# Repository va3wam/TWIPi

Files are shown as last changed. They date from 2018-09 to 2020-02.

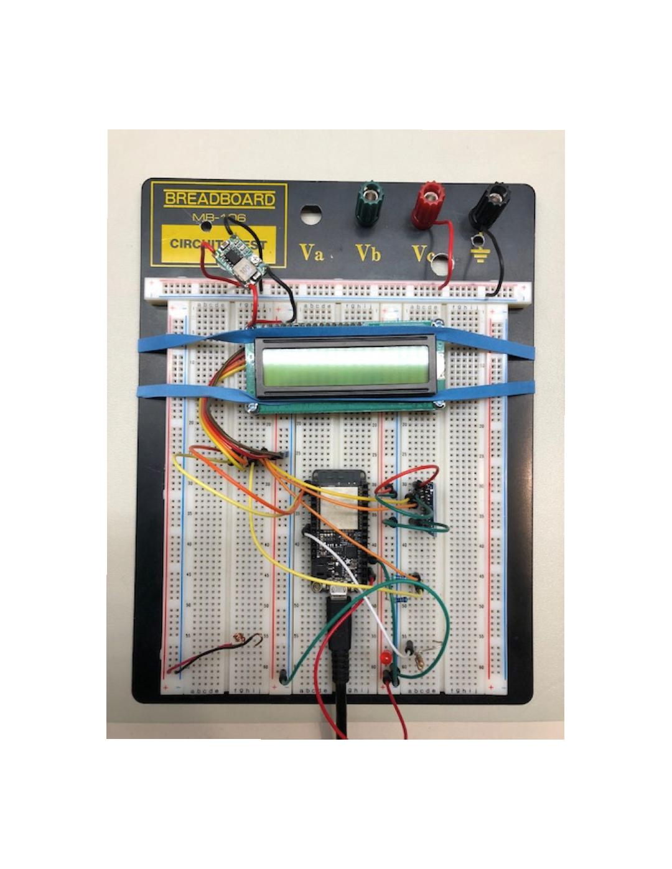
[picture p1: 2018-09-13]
img/SegbotStepMARK3.jpg

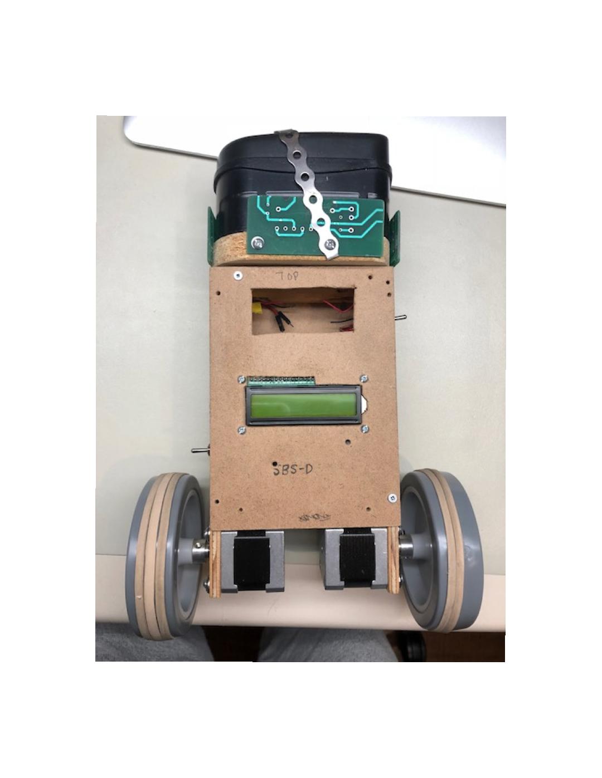
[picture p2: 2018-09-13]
img/SegbotStepMARK2.jpg

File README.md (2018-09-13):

# TWIPi
This repository contains all the information on the fourth iteration of the SegbotSTEP family of robot designs. This repository contains C++ source code intended to run on the Adafruit Huzzah32 development board; Java code intended to run on a remote client such as a MAC or PC; EagleCAD schematic and layout files containing the circuit designs of the robot; Fusion 360 files (or pointers to those files on the AutoCAD cloud) used to mill the robot chassis; and all the libraries used by the IDEs that make up the tool chain used to create the robot.  

## Getting Started

Full details about this project can be read on our [wiki](https://github.com/va3wam/TWIPi/wiki). 

### Prerequisites

In order to make use of the robot circuit board and schematic diagrams you will need AutoCAD's EagleCAD application. In order to make use of the CAD and CAM diagrams of the robot chassis you will need AutoCAD's Fusion 360 application. From a software perspective, the Java and C++ (Arduino) code was written using Microsoft's Visual Source Code IDE.

### SOC Hardware Compatability

The Arduino C++ code was written to run on the Espressif ESP WROOM32 "Software On a Chip" (SOC). The development board used for this SOC is the Adafruit Huzzah32 featherboard.  

```
Note that this code will NOT run on an ESP8266. 
```

### Other Hardware Compatability

Aside from the code and development you will need to build a TWIPi compatible chassis and PCB. This
repository has EagleCAD diagrams to help you build the PCB. Also included are Fusion360 
CAD/CAM diagrams and associated GCODE for a Tormach 770 CNC mill to create the robot chassis. 
Full details for this project are located on the wiki associated with this repository.

### Installing

There are numerous tutorials on how to install Arduino code onto an ESP WROOM32 from Visual Source Code. Details and relevant links can be found on this respositories wiki. 

## Running the tests

At this time there are no automated tests for this system

## Deployment

This Arduino code was developed using the following set up.

### Built With

* [Visual Studio Code](https://code.visualstudio.com/) - The IDE
* [Platformio](https://platformio.org/) - Editor plugin
* Library Framework - Arduino
* Hardware platform - espressif32
* Board - Adafruit Huzzah32 featherboard
### Arduino Libraries
The following additional libraries are used in the Arduino C++ code:
* https://github.com/Pedroalbuquerque/ESP32WebServer
* https://github.com/Links2004/arduinoWebSockets
* https://github.com/marcoschwartz/LiquidCrystal_I2C
* https://github.com/bblanchon/ArduinoJson

## Contributing

This project is being developed by a couple of buddies. We are tracking the tasks for this
effort in a series of small [projects](https://github.com/va3wam/TWIPi/projects).

## Versioning

We use [SemVer](http://semver.org/) for versioning. For the versions available, see the [tags on this repository](https://github.com/va3wam/TWIPi/branches/all). 

## Authors

* [Doug](https://github.com/nerdoug) - *PID and motor control logic and circuit diagrams*
* [Andrew](https://github.com/va3wam) - *Initial code porting from ESP128 to ESP32, remote Java client and CAD/CAM designs* 

See also the list of [contributors](https://github.com/va3wam/TWIPi/graphs/contributors) who participated in this project.

## License

This project has no licensing terms. Use at own risk, no support provided. 

## Acknowledgments

* Big thanks to [Brokking](http://www.brokking.net/yabr_main.html) for his excellent tutorial which really helped us get going
* Thanks to the folks who developed the libraries we have made use of for I2C, JSON, Web and Websockets

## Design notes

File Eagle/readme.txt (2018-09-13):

This is the directory where PCB files are placed

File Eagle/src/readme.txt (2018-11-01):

This is where the Schematic (SCH) and Layout (BRD) files for Eagle PCBs go. the file testToolOffsetModForFlatCAMfiles.nc contains manually crafted g-code to test ATC control for jobs created in FlatCAM. See TWIPi\Eagle\docConvertFlatCAMgcode.ods for the procedure for inserting these codes into FlatCAM generated G-code.

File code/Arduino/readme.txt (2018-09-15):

This is where c++ code intended to run on the Arduino compliant SOC goes

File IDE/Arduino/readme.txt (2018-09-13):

This is where Arduino IDE configuration and library files go

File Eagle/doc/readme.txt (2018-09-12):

This directory contains the PCB files associated with the TWIPi project

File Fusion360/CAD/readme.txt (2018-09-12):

This directory contains the CAD files associated with the TWIPi project

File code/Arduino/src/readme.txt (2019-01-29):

This is where the C++ code loaded onto the ESP32 inside the robot is located.

TWIPi directory has the code to be loaded onto the ESP32 that runs the TWIPi robot
BlinkLED directory has code that blinks the software controlled LED (white) on the TWIPi peripheral board
LCD16x2Test directory has code that prints "HELLO WORLD" on TWIPi's LCD
two-I2C-scan directory has code that scans the two I2C buses for active devices

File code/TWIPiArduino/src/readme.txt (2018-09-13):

This is where the C++ code loaded onto the ESP32 inside the robot is located.

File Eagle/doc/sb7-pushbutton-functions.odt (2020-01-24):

Twipi Pushbutton Functions

Layout:

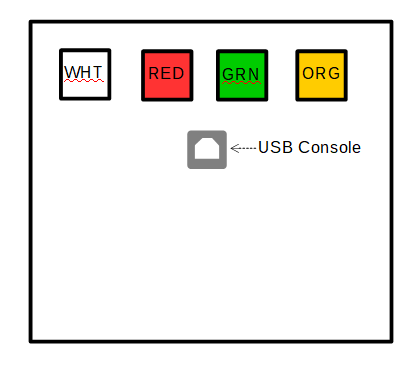
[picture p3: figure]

Functions

Button Colour | Pushed In | Out Position | Illuminated | Extinguished
White | Battery Power CONNECTED | Battery power DISCONNECTED | 12 V power IS available | 12 V power IS NOT available
Red | 5 v power comes from BATTERY | 5 v power comes from USB Console | 5 V battery power IS available | 5 V battery power is NOT available
Green | ESP32 is being RESET | ESP32 is NOT being RESET | Selected 5 V power is going to ESP32 | Selected 5 V power is NOT going to ESP32
Orange | S/W readable pin is HIGH | S/W readable pin is LOW | S/W has turned ON the light | S/W has turned OFF the light

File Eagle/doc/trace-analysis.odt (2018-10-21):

Examination of Etch Widths In Eagle > FlatCAM > G-CodeFiles

Test files:

etch-fun.sch, etch-fun.brd

-Eagle files for minimal circuiit to simplify analysis

tst1-trace-by-wiki.nc, tst1-drill-by-wiki.nc

-G-Code files produced from etch-fun files by following procedure and parameter settings in our wiki.

- parameter settings are documented in the cad-conversions.ods file as well

chart-data.ods

- import of trace file G-Code corners into a spreadsheet

- charted using a scatter graph to allow examination of data points from the shapes

The bottom right corner of the circuit has a trace running between the larger of the pads which seems like a good case to examine. The scatter graph for that part looks like this:

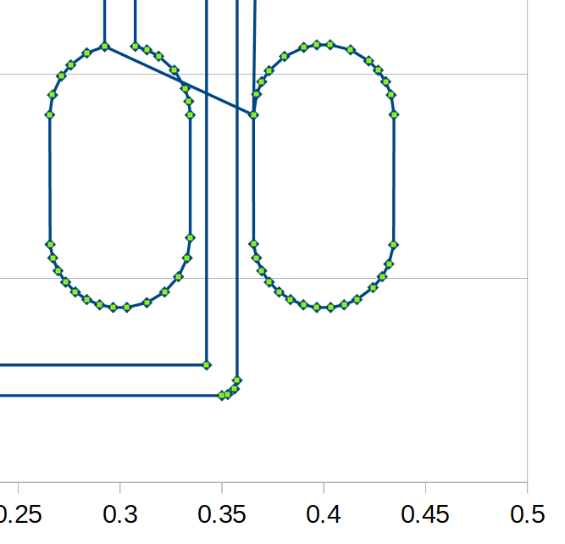
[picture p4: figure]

The cross section of the vertical trace looks like this:

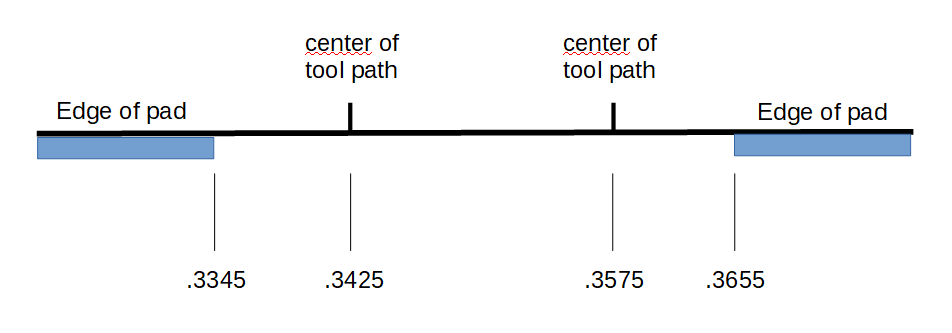
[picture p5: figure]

Adding the 0.009 inch width of the V bit to the diagram, we get:

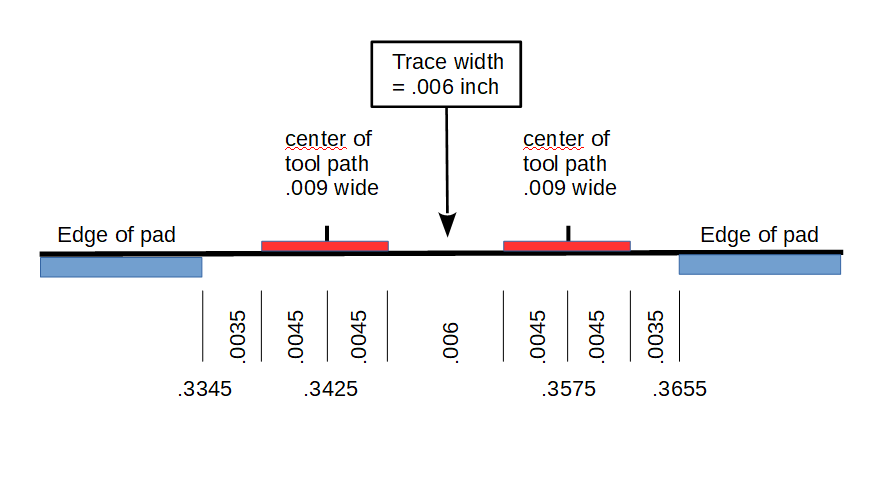
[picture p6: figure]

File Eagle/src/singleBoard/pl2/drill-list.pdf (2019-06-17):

Sheet1

Page 1

Component / Package | Comment
Board Mounting holes | 1 | 4 | 2.845 | 112 | 0.112 | 4 | A
Power cable headers | 2 | 2 | 1.016 | 40 | 0.04 | 4 | B
Ribbon cable connector | 1 | 16 | 0.9144 | 36 | 0.036 | 16 | B
Pushbutton switches | 4 | 5 | 1.2 | 47.2 | 0.0472 | 20 | C
USB Jack | 1 | 4 | 0.92 | 36.2 | 0.0362 | 4 | B | cable pins
USB Jack | 1 | 2 | 2.3 | 90.6 | 0.0906 | 2 | A | mounting lugs
Diodes | 2 | 2 | 1.4986 | 59 | 0.059 | 4 | D
1 pin headers / Vias | 13 | 1 | 1 | 39.4 | 0.0394 | 13 | B
total holes: | 67
Suggested Drill Sizes in column H: | A | 112 mils
| | | B | 38 mils
| | | C | 47 mils
| | | D | 59 mils

`

Component
Qty

Holes per
component

Hole size
mm

Hole size
mils

Hole size
inches

total
hole count

Standard
-ized

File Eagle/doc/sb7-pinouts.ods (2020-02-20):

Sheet: ESP32 connections
PINOUTS FOR THE Adafruit ESP32 Feather Module in the TWIPi Single Board Version 7 (SB7)
Adafruit ESP32 Phys. pin | Gpio | Pin Function (A/D, I2C, SPI, serial...) | Connection in the Single Board Version 3 (SB3)
1 |  | RESET | XB1 - Reset switch - to Normally Open (NO) on 3rd pushbutton (green)
2 |  | 3V | P6 on both DRV’s (JP19>JP15, JP20>JP16),IMU Vcc, IMU I2C pullups, CPU & IMU decoupling cap,XB2
3 |  | n/c
4 |  | CPU GND | Bridged GNDs: battery gnd, 12V, 5V bat., 5V USB, ESP-USB, DRV, CPU & IMU decoupl, XB12 & 14, LCD, Mosfet
5 | 26 | A0, GPio26 | n/c
6 | 25 | A1, GPio25 A/D | (A/D input) to centre between the 2 resistors of the MOSFET controlled voltage divider
7 | 34 | A2, GPio34 | n/c
8 | 39 | A3, GPio39 | INT pin on IMU - generates an interrupt
9 | 36 | A4, GPio36 | n/c
10 | 4 | A5, GPio4 | XB3 software-readable pushbutton input, to COM position on 4th pushbutton
11 | 5 | SPI-SCK, GP05 | MOSFET enable on battery monitor (Gate)
12 | 18 | SPI-MO | DRV1-STEP
13 | 19 | SPI-MI | DRV1-DIR
14 | 16 | RX Serial1 | DRV1-ENA
15 | 17 | TX Serial1 | I2C-IMU Pin4, SDA with 2.2K pullup to 3.3V
16 | 21 | GPio21 | I2C-IMU Pin3, SCL with 2.2K pullup to 3.3V
17 | 23 | I2C, GP23 | XB4 > software controlled LED, +ve LED input on 4th pushbutton (orange)
18 | 22 | I2C, GP22 | I2C-LCD-SDA-P2 (4.7K pullup to 5V)
19 | 14 | A6, GPio14 | I2C-LCD-SCL-P1 (4.7K pullup to 5V)
20 | 32 | A7, GPio32 | DRV2-FAULT Input (used to be VDD on old A4988)
21 | 15 | A8, GPio15 | DRV2-DIR
22 | 33 | A9, GPio33 | DRV2-STEP
23 | 27 | A10, GPio27 | DRV2-ENA
24 | 12 | A11, GPio12 | N/C. Using this pin seems to prevent software download in some circumstances
25 | 13 | A12, GPio13 | DRV1-FAULT Input. (used to be VDD on old A4988)
26 |  | USB | +5 Volts, LCD-I2C pullups, LCD header
27 |  | Enable | n/c
28 |  | LiPo Battery | n/c
 | (A13,GPio35) resistor divider linked to VBAT
 |  |  | fully programmable weak pullup / pulldown ( 14, 16, 17, 18, 19, 21, 22, 23)
 |  |  | powers up with weak pullUP enabled ( 5, 15)
 |  |  | powers up with weak pullDOWN enabled ( 4)
 |  |  | input only pins ( 34, 36, 39)
 |  |  | can be touch capacitive sensor ( 10, 19, 20, 21, 22, 23, 24, 25)
DRV stands for the DRV8825 stepper motor controllers. DRV1 is the top DRV (closest to IMU), DRVR is the bottom DRV,

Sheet: MB LCD Header
LCD Header on Main Board
 | LCD Hdr - 1 | SCL
 | LCD Hdr - 2 | SDA
 | LCD Hdr - 3 | 5 V
 | LCD Hdr - 4 | GND
 | above agrees with order of pins on standard LCD 1602

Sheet: MB CPU Console USB Cable
CPU Console USB cable - Micro USB to 4 pin header on MB
Actual | Standard | Pin # | Function
ORG | RED | MB-USB-Hdr-1 | IBC22 - +5 Common
YEL | WHT | MB-USB-Hdr-2 | IBC23 - USB Jack - 2 - D-
GRN | GRN | MB-USB-Hdr-3 | IBC24 - USB Jack - 3 - D+
BLU | BLK | MB-USB-Hdr-4 | IBC25 - Gnd Common

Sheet: USB Reference
reference: http://www.hobbytronics.co.uk/usb-connector-pinout

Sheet: Standard LCD 1602 I2C Wiring
 |  | ------- | GND
 |  | ------- | 5 V
 |  | ------- | SDA
 |  | ------- | SCL
 | Back View
Industry standard pinout for LCD 1602 I2C interface.
sample references:
http://wiki.sunfounder.cc/index.php?title=I%C2%B2C_LCD1602
https://opencircuit.nl/ProductInfo/1000061/I2C-LCD-interface.pdf

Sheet: MPU-6050
http://acoptex.com/project/118/basics-project-020a-mpu-6050-gy-521-gy-521-module-3-axis-gyroscope-and-accelerometer-at-acoptexcom/
 | MPU-6050 is mounted on the GY-521 board with:
 | -MPU-6050 on component side of board, in about the center
 | - the +Y axis pointing towards short side of board touching Vcc
 | - the +X axis pointing towards the long side of the board closest to the mounting holes
 | - the +Z axis pointing upwards, perpendicular to the component side
 | - the label text on the MP-6050 chip is in the same direction as the Vcc label in the silkscreen
 | in MB2 hardware, the IMU is mounted “upside down, and rotated”:
 | +Y axis pokes out of robot's chest
 | +X axis pokes out of bot's right shoulder (viewer's left)
 | +Z axis points towards ground
 | The pins leave the IMU on the solder side of the board, not the side with the IMU
 | - the label text on the MP-6050 chip is in the same direction as the Vcc label in the silkscreen

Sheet: pushbutton wiring
See other stand alone documents

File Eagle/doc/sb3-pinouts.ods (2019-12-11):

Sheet: ESP32 connections
PINOUTS FOR THE Adafruit ESP32 Feather Module in the TWIPi Single Board Version 3 (SB3)
Adafruit ESP32 Phys. pin | Gpio | Pin Function (A/D, I2C, SPI, serial...) | Connection in the Single Board Version 3 (SB3)
1 |  | RESET | XB1 - Reset switch
2 |  | 3V | P6 on both DRV’s (JP19>JP15, JP20>JP16),IMU Vcc, IMU I2C pullups, CPU & IMU decoupling cap,XB2
3 |  | n/c
4 |  | CPU GND | Bridged GNDs: battery gnd, 12V, 5V bat., 5V USB, ESP-USB, DRV, CPU & IMU decoupl, XB12 & 14, LCD, Mosfet
5 | 26 | A0, GPio26 | n/c
6 | 25 | A1, GPio25 A/D | (A/D input) JP2 > JP1 > MOSFET controlled voltage divider
7 | 34 | A2, GPio34 | n/c
8 | 39 | A3, GPio39 | n/c
9 | 36 | A4, GPio36 | n/c
10 | 4 | A5, GPio4 | XB3 software-readable puchbutton input
11 | 5 | SPI-SCK, GP05 | DRV1-ENA (powers up with WPD enabled)
12 | 18 | SPI-MO | DRV1-STEP
13 | 19 | SPI-MI | DRV1-DIR
14 | 16 | RX Serial1 | MOSFET enable on battery monitor
15 | 17 | TX Serial1 | I2C-IMU Pin4, SDA with 2.2K pullup to 3.3V
16 | 21 | GPio21 | I2C-IMU Pin3, SCL with 2.2K pullup to 3.3V
17 | 23 | I2C, GP23 | XB4 > software controlled LED
18 | 22 | I2C, GP22 | I2C-LCD-SDA-P1 (4.7K pullup to 5V)
19 | 14 | A6, GPio14 | I2C-LCD-SCL-P2 (4.7K pullup to 5V)
20 | 32 | A7, GPio32 | DRV2-FAULT Input
21 | 15 | A8, GPio15 | DRV2-DIR
22 | 33 | A9, GPio33 | DRV2-STEP
23 | 27 | A10, GPio27 | DRV2-ENA
24 | 12 | A11, GPio12 | DRV1-FAULT Input. Trace to ESP Pin 24 was cut because it prevented code download. Could use pin 7, 8 or 9
25 | 13 | A12, GPio13 | n/c
26 |  | USB | +5 Volts, LCD-I2C pullups, LCD header
27 |  | Enable | n/c
28 |  | LiPo Battery | n/c
 | (A13,GPio35) resistor divider linked to VBAT
 |  |  | fully programmable weak pullup / pulldown ( 14, 16, 17, 18, 19, 21, 22, 23)
 |  |  | powers up with weak pullUP enabled ( 5, 15)
 |  |  | powers up with weak pullDOWN enabled ( 4)
 |  |  | input only pins ( 34, 36, 39)
 |  |  | can be touch capacitive sensor ( 10, 19, 20, 21, 22, 23, 24, 25)
DRV stands for the DRV8825 stepper motor controllers. DRV1 is the top DRV (closest to IMU), DRVR is the bottom DRV,

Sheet: TWIPi External Switches Connector
PINOUTS for the 16 pin External Switch Connector (XB)
Physical Pin | Pushbutton function name | Function
XB1 | PC8 | ESP32 Reset Pin
XB2 | PC10 | 3.3 V
XB3 | PC11 | s/w readable switch input on ESP10, GPio4
XB4 | PC9 | s/w controlled LED on ESP17, GPio23
XB5 | PC1 | thru resistor to 12V for LED monitor
XB6 | KEY | unused. blocked to prevent incorrect insertion
XB7 | PC5 | 5V from regulator, for monitor LED
XB8 | PC6 | 5V from USB jack
XB9 | PC7 | to ESP32 USB 5V
XB10 | UJ1 | USB Jack pin 1
XB11 | UJ2 | USB Jack pin 2
XB12 | PC4 | Ground
XB13 | UJ3 | USB Jack pin 3
XB14 | UJ4 | USB Jack pin 4
XB15 | PC2 | Battery’s positive side 20+ Volts

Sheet: MB LCD Header
LCD Header on Main Board
 | LCD Hdr - 1 | SCL (pin 1 nearest ESP32)
 | LCD Hdr - 2 | SDA
 | LCD Hdr - 3 | 5 V
 | LCD Hdr - 4 | GND
 | above agrees with order of pins on standard LCD 1602

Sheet: MB CPU Console USB Cable
CPU Console USB cable - Micro USB to 4 pin header on MB
Actual | Standard | Pin # | Function
ORG | RED | MB-USB-Hdr-1 | IBC22 - +5 Common
YEL | WHT | MB-USB-Hdr-2 | IBC23 - USB Jack - 2 - D-
GRN | GRN | MB-USB-Hdr-3 | IBC24 - USB Jack - 3 - D+
BLU | BLK | MB-USB-Hdr-4 | IBC25 - Gnd Common

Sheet: USB Reference
reference: http://www.hobbytronics.co.uk/usb-connector-pinout

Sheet: Standard LCD 1602 I2C Wiring
 |  | ------- | GND
 |  | ------- | 5 V
 |  | ------- | SDA
 |  | ------- | SCL
 | Back View
Industry standard pinout for LCD 1602 I2C interface.
sample references:
http://wiki.sunfounder.cc/index.php?title=I%C2%B2C_LCD1602
https://opencircuit.nl/ProductInfo/1000061/I2C-LCD-interface.pdf

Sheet: MPU-6050
http://acoptex.com/project/118/basics-project-020a-mpu-6050-gy-521-gy-521-module-3-axis-gyroscope-and-accelerometer-at-acoptexcom/
 | MPU-6050 is mounted on the GY-521 board with:
 | -MPU-6050 on component side of board, in about the center
 | - the +Y axis pointing towards short side of board touching Vcc
 | - the +X axis pointing towards the long side of the board closest to the mounting holes
 | - the +Z axis pointing upwards, perpendicular to the component side
 | - the label text on the MP-6050 chip is in the same direction as the Vcc label in the silkscreen
 | in MB2 hardware, the IMU is mounted “upside down, and rotated”:
 | +Y axis pokes out of robot's chest
 | +X axis pokes out of bot's right shoulder (viewer's left)
 | +Z axis points towards ground
 | The pins leave the IMU on the solder side of the board, not the side with the IMU
 | - the label text on the MP-6050 chip is in the same direction as the Vcc label in the silkscreen

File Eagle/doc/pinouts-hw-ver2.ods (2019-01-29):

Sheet: ESP32 connections
PINOUTS FOR THE Adafruit ESP32 Feather Module Version 3
Adafruit ESP32 Phys. pin | Gpio | Pin Function (A/D, I2C, SPI, serial...) | Connection
1 |  | RESET | IBC24 - Reset switch
2 |  | 3V | P10 on both DRV’s,IMU Vcc, IMU I2C pullups, IMU decoupling cap
3 |  | n/c
4 |  | CPU GND | Bridged GNDs: battery gnd, 12V, 5V bat., 5V USB, ESP32, DRV
5 | 26 | A0, GPio26 | n/c
6 | 25 | A1, GPio25 A/D | (A/D input) JP2 > JP4 > IBC12 > MOSFET controlled voltage divider
7 | 34 | A2, GPio34 | n/c
8 | 39 | A3, GPio39 | n/c
9 | 36 | A4, GPio36 | n/c
10 | 4 | A5, GPio4 | DRVR-ENA (powers up with WPD enabled)
11 | 5 | SPI-SCK, GP05 | JP1 > JP3 > IBC13 > MOSFET enable on battery monitor
12 | 18 | SPI-MO | DRVR-STEP
13 | 19 | SPI-MI | DRVR-DIR
14 | 16 | RX Serial1 | IBC-12 Software readable sense switch (Reset switch held left)
15 | 17 | TX Serial1 | I2C-IMU Pin4, SDA with 2.2K pullup to 3.3V
16 | 21 | GPio21 | I2C-IMU Pin3, SCL with 2.2K pullup to 3.3V
17 | 23 | I2C, GP23 | IBC11 > software controlled LED
18 | 22 | I2C, GP22 | I2C-LCD-SDA-P1 (4.7K pullup to 5V)
19 | 14 | A6, GPio14 | I2C-LCD-SCL-P2 (4.7K pullup to 5V)
20 | 32 | A7, GPio32 | DRVL-DIR
21 | 15 | A8, GPio15 | DRVL-STEP
22 | 33 | A9, GPio33 | DRVL-ENA
23 | 27 | A10, GPio27 | n/c
24 | 12 | A11, GPio12 | n/c
25 | 13 | A12, GPio13 | n/c
26 |  | USB | +5 Volts
27 |  | Enable | n/c
28 |  | LiPo Battery | n/c
 |  | (A13,GPio35) resistor divider linked to VBAT
 |  | fully programmable weak pullup / pulldown ( 14, 16, 17, 18, 19, 21, 22, 23)
 |  | powers up with weak pullUP enabled ( 5, 15)
 |  | powers up with weak pullDOWN enabled ( 4)
 |  | input only pins ( 34, 36, 39)
 |  | can be touch capacitive sensor ( 10, 19, 20, 21, 22, 23, 24, 25)
 |  | DRV stands for the DRV8825 stepper motor controllers (one rotated 180 degrees to simplify circuit layout)
 |  | DRVL is the left DRV, closest to the ESP32. DRVR is the right DRV, closest to the CPU USB header

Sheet: TWIPi InterBoard Connector
 |  | 2018-12-28
PINOUTS for the 25 pin InterBoard Connector (IBC)
25 Pin IBC for PB1A | Pin Function | Connection
1 | 12 V power | Cap1pos-DRVR-VMOT-P16
2 | stepper coil | DRVL-1B-P11
3 | stepper coil | DRVL-1A-P12
4 | stepper coil | DRVL-2A-P13
5 | stepper coil | DRVL-2B-P14
6 | 12 V power | Cap2pos-DRVL-VMOT-P16
7 | 12V GND | Cap2neg-DRVL-MGND-P15
8 | n/c
9 | battery A2D | Vdivider >IBC9 >JP4 >JP2 >ESP6 = A2D A1
10 | MOSFET Enable | Mosfet Gate >IBC10 >JP3 >JP1 > ESP11 = GPio5
11 | s/w controlled LED | CPU-GPio 23, pin 17
12 | s/w sense switch | Reset switch-left-pos > IBC12 > ESP14 = GPio16
13 | RESET | Reset switch-right-pos >IBC13 > CPU-P1
14 | 12V GND | Cap1neg-DRVR-MGND-P15
15 | n/c
16 | n/c
17 | n/c
18 | stepper coil | DRVR-2B-P14
19 | stepper coil | DRVR-2A-P13
20 | stepper coil | DRVR-1A-P12
21 | stepper coil | DRVR-1B-P11
22 | 5V Source Selected | USB JACK Pin1 +5V gets to CPU USB HDR - P1
23 | USB Data | USB JACK Pin2 D-, gets to CPU USB HDR - P2
24 | USB Data | USB JACK Pin3 D+ , gets to CPU USB HDR - P3
25 | USB Ground | USB JACK Pin4 Gnd, gets to CPU USB HDR - P4

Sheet: MB LCD Header
LCD Header on Main Board
 | LCD Hdr - 1 | SCL (pin 1 nearest ESP32)
 | LCD Hdr - 2 | SDA
 | LCD Hdr - 3 | 5 V
 | LCD Hdr - 4 | GND
 | above agrees with order of pins on standard LCD 1602
 | (unlike MB1, which had SDA and SCL reversed)

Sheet: MB CPU Console USB Cable
CPU Console USB cable - Micro USB to 4 pin header on MB
Actual | Standard | Pin # | Function
ORG | RED | MB-USB-Hdr-1 | IBC22 - +5 Common
YEL | WHT | MB-USB-Hdr-2 | IBC23 - USB Jack - 2 - D-
GRN | GRN | MB-USB-Hdr-3 | IBC24 - USB Jack - 3 - D+
BLU | BLK | MB-USB-Hdr-4 | IBC25 - Gnd Common

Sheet: USB Reference
reference: http://www.hobbytronics.co.uk/usb-connector-pinout

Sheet: Standard LCD 1602 I2C Wiring
 |  | ------- | GND
 |  | ------- | 5 V
 |  | ------- | SDA
 |  | ------- | SCL
 | Back View
Industry standard pinout for LCD 1602 I2C interface.
sample references:
http://wiki.sunfounder.cc/index.php?title=I%C2%B2C_LCD1602
https://opencircuit.nl/ProductInfo/1000061/I2C-LCD-interface.pdf

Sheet: MPU-6050
http://acoptex.com/project/118/basics-project-020a-mpu-6050-gy-521-gy-521-module-3-axis-gyroscope-and-accelerometer-at-acoptexcom/
 | MPU-6050 is mounted on the GY-521 board with:
 | -MPU-6050 on component side of board, in about the center
 | - the +Y axis pointing towards short side of board touching Vcc
 | - the +X axis pointing towards the long side of the board closest to the mounting holes
 | - the +Z axis pointing upwards, perpendicular to the component side
 | - the label text on the MP-6050 chip is in the same direction as the Vcc label in the silkscreen
 | in MB2 hardware, the IMU is mounted “upside down, and rotated”:
 | +Y axis pokes out of robot's chest
 | +X axis pokes out of bot's right shoulder (viewer's left)
 | +Z axis points towards ground
 | The pins leave the IMU on the solder side of the board, not the side with the IMU
 | - the label text on the MP-6050 chip is in the same direction as the Vcc label in the silkscreen

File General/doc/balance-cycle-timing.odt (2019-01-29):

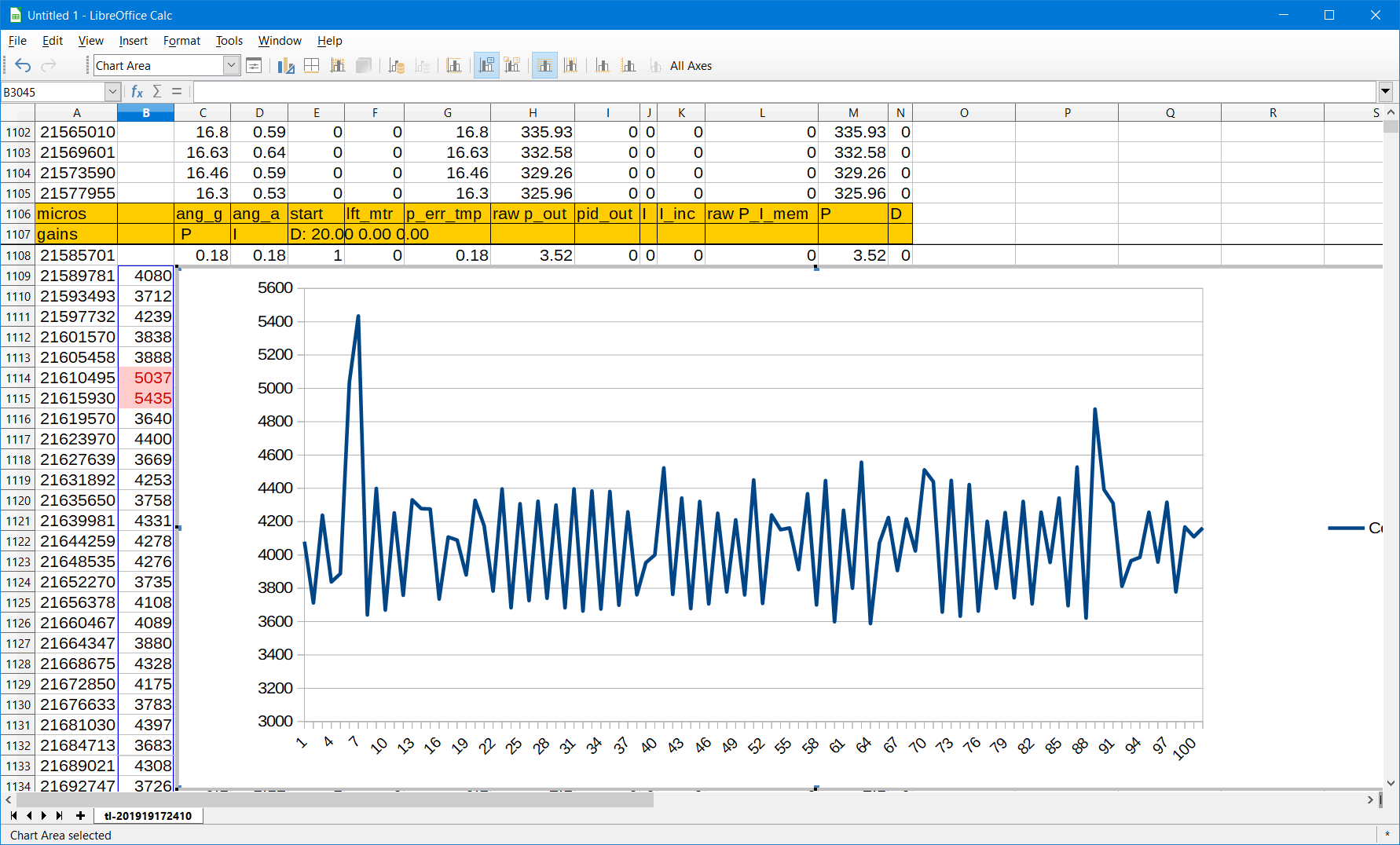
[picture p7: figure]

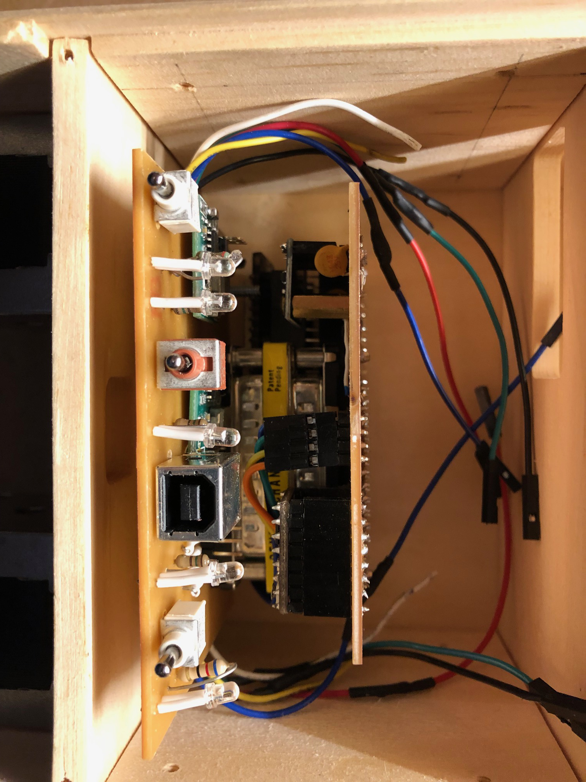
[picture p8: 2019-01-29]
img/boardsinChassis.jpg

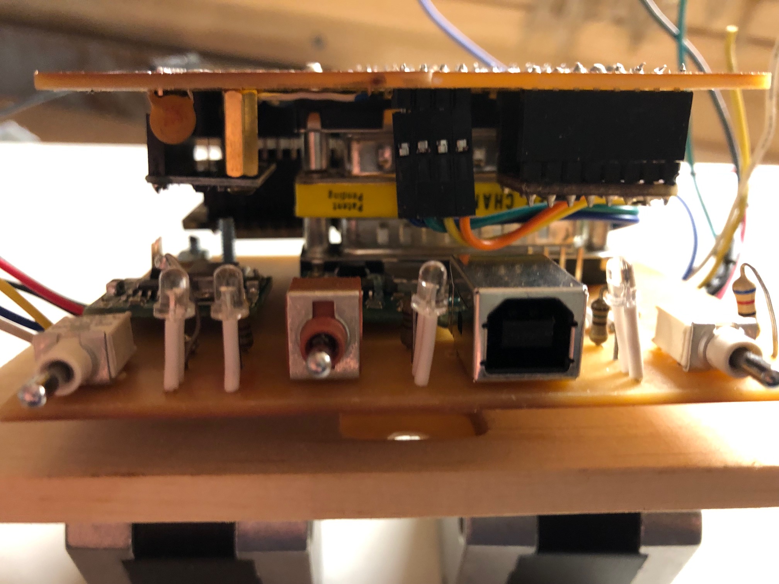
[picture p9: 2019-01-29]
img/boardsConnected.jpg

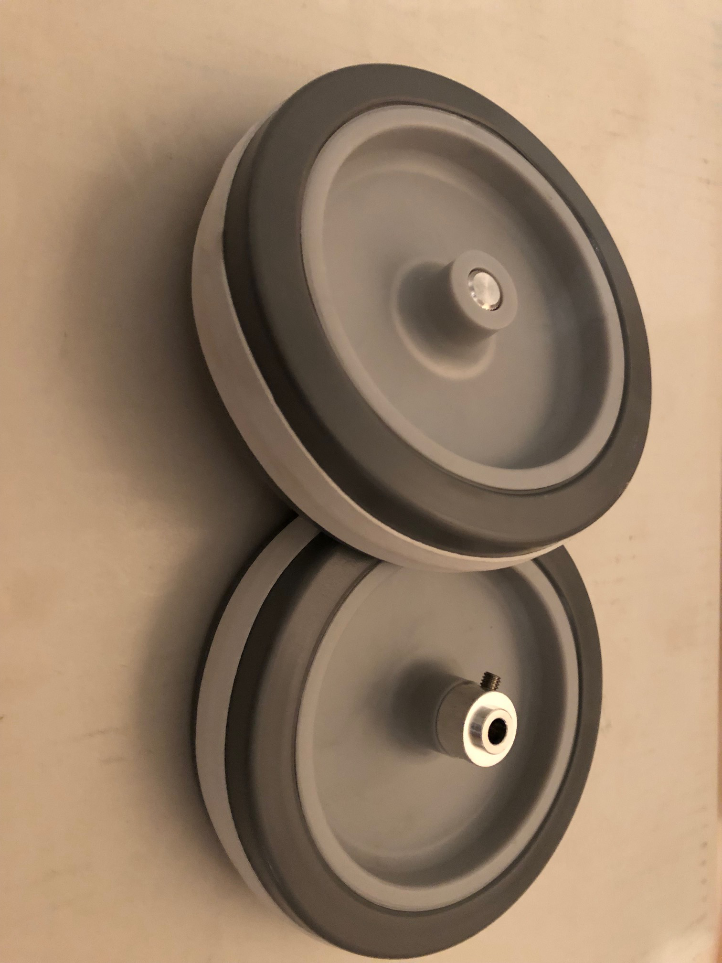
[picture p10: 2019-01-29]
img/wheels.jpg

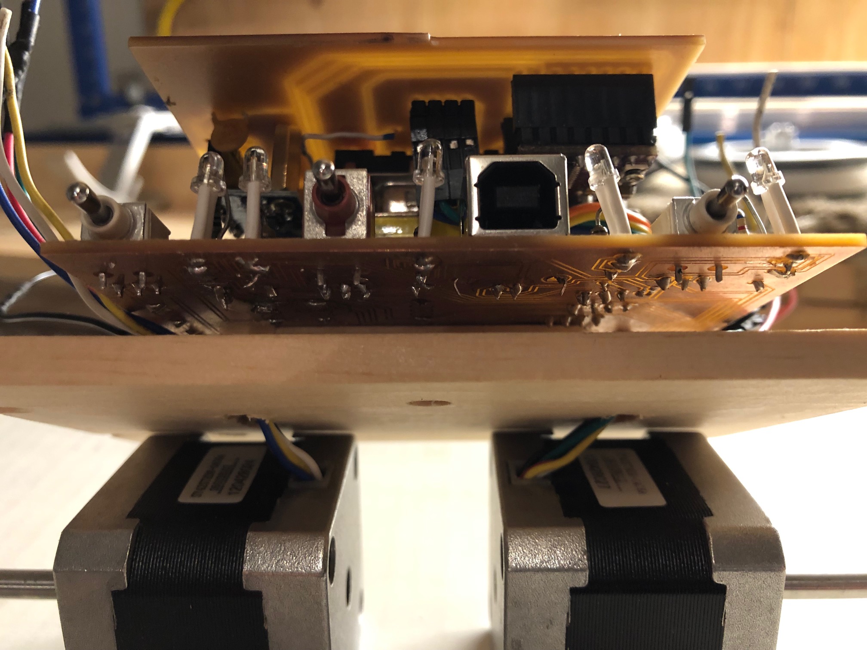
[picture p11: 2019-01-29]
img/motorsMounted2.jpg

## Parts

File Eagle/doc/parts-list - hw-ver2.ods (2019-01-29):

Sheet: Summary
Parts List for A single TWIPi Robot, version 2 hardware
Ref | MB2 Qty | PB2 Qty | On hand | Qty to buy | Description | DigiKey Part | DigiKey Unit Cost | Mouser Part | Mouser Unit Cost
 | 1 |  |  |  | Main Board Printed Circuit Board
 | 1 |  |  |  | Adafruit Huzzah ESP-32 Feather
 | 1 |  |  |  | 12 pin female header to mount ESP-32
 | 1 |  |  |  | 16 pin female header to mount ESP-32
 | 1 |  |  |  | ESP-32 console cable: Micro USB - female pins
 | 1 |  |  |  | IMU with mounting bolts and standoffs
 | 2 |  |  |  | IMU set of 4 mounting bolts and 2 standoffs each
 | 1 |  |  |  | 8 pin female headers to mount IMU
 | 1 | 1 |  |  | 25 pin sub-D connector, female
 | 1 |  |  |  | 25 male/male gender mender
 | 2 |  |  |  | DRV8825 Bipolar Stepper Motor controller
 | 4 |  |  |  | 8 pin female headers to mount DRV8825s
 | 2 |  |  |  | 4 pin male header (LCD and CPU USB)
 | 1 |  |  |  | 4 conductor female/female LCD cable
 | 2 |  |  |  | 2.2K pullup resistors
 | 2 |  |  |  | 4.7K pullup resistors
 | 3 |  |  |  | .1 uF decoupling capacitors
 | 2 |  | 2 |  | jumper wires JP1-3, JP2-4
 | MB2 Qty | PB2 Qty | Qty on hand |  | Description | DigiKey Part | DigiKey Unit Cost | Mouser Part | Mouser Unit Cost
 |  | 1 |  |  | Peripheral Board Printed Circuit Board
 |  | 3 |  |  | SPDT edge mount switch (power, 5V, reset))
 |  | 1 |  |  | resistors for PB LEDs - 12V =580+ Ohm
 |  | 3 |  |  | resistors for PB LEDs - 5V =213,213,113
 |  | 1 |  |  | resistors for PB LEDs - 3.3V =
 |  | 5 | 5 |  | edge mount LEDs, various colours
 |  | 1 |  |  | USB type B edge mount jack
 |  | 1 |  |  | 3 pin male header (PB power) right angle?
 |  | 2 |  |  | step down power regulator
 |  | 2 |  |  | 4 pin male header (stepper coil wires) (rt angle?)
 |  | 1 |  |  | MOSFET battery monitoring enable | IRFD9120PBF-ND | 1.61
 |  |  |  |  | voltage divider high resistor
 |  |  |  |  | voltage divider low resistor
 |  |  |  |  | voltage divider capacitor
 |  |  |  |  | MOSFET pullup resistor
 | MB2 Qty | PB2 Qty | Qty on hand |  | Description | DigiKey Part | DigiKey Unit Cost | Mouser Part | Mouser Unit Cost
 |  | 2 |  |  | wheels
 |  | 2 |  |  | rubber band wheel tires
 |  | 2 |  |  | stepper motors with mounting bolts and washers
 |  | 1 |  |  | parts for battery power harness
 |  | 8 |  |  | parts to put connectors on stepper coil wires
 |  | 1 |  |  | screws for chassis
 |  | 1 |  |  | wood for chassis
 |  | 1 |  |  | battery subassembly
 |  | 1 |  |  | 2 x 16 LCD display with I2C controller

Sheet: Notes
Twipi Part | Supplier | Mfr Part Number | Mouser Part Number | Cost | Details | QTY | Comments
25 pin connector
 | digikey | only has right angle: Amphenol 6E17C-02S-AJ-120-ND
 |  | not sure if footprint is OK
 | mouser canada | seems to have lots | differences may be level of gold plating on contacts
 |  | D25S24A4GV00LF | 649-D25S24A4GV00LF | 4
 |  | KF85X-BD-25S-BR | 806-KF85X-BD-25S-BR | 14.74
 |  | 5745922-2 | 571-5745922-2 | 23.24
 |  | D25S24B6GV00LF | 649-D25S24B6GV00LF | 4.2 |  | 6
 |  | 164A16639X | 706-164A16639X | 14.68
 |  | chart:
 |  | https://www.mouser.ca/Connectors/D-Sub-Connectors/D-Sub-Standard-Connectors/_/N-9gybx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
SPDT | Mouser canada | ET03MD1ABE | 611-ET03-011 | 10.89 |  | 6
DPDT |  | ET23MD1ABE | 611-ET23MD1ABE | 16.08 |  | 3
USB JACK |  | E8144-B02022-L | 673-E8144B02022L | 1.06 |  | 3
LED |  | 5352T1-5VLC | 607-5352T1-5VLC | 4.11 | red
 |  | 5350T1 | 607-5350T1 | 2.93
 |  | SSF-LXH555GD | 696-SSF-LXH555GD | 1.42 | green | 10 | relampable
 |  | SSF-LXH555YD | 696-SSF-LXH555YD | 1.42 | yellow | 10
 |  | SSF-LXH555ID | 696-SSF-LXH555ID | 1.41 | red | 10

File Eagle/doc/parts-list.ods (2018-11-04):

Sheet: Summary
 |  | Parts List for TWIPi Robot |  |  | Ver 2 / 2018-10-30
Board | Qty needed | Qty on hand | Qty to buy | Source | Description | DE | AM | Get | Comment
MB | 1 |  |  | CNC | Main Board Printed Circuit Board |  | 1
MB | 1 | 1 |  | DE | Adafruit Huzzah ESP-32 Feather | 1
MB | 1 |  |  | DE | 12 pin female header to mount ESP-32 | 1
MB | 1 |  |  | DE | 16 pin female header to mount ESP-32 | 1
MB | 1 |  |  | ? | ESP-32 console cable: Micro USB - female pins |  |  |  | need to build
MB | 1 |  |  | ? | IMU with mounting bolts and standoffs
MB | 1 |  |  | Richard | 8 pin female headers to mount IMU | 1 |  |  | Have 1 soldered on proto board
MB | 2 |  |  | Mouser | 25 pin sub-D connector, female
MB | 2 |  |  | DE | DRV8825 Bipolar Stepper Motor controller | 4
MB | 4 |  |  | Richard | 8 pin female headers to mount DRV8825s |  |  |  | Have 4 soldered on proto board
MB | 2 |  |  | DE | 4 pin male header (LCD and CPU USB) | 2 |  |  | to be separated
MB | 1 |  |  | DE | 4 conductor female/female LCD cable | 1
MB | 4 |  |  | DE | 2.2K pullup resistors | 4 |  |  | 2.7K actually
MB | 3 |  |  | DE | .1 uF decoupling capacitors | 3 |  |  | Cap label = 104, have a variety
 | Qty needed | Qty on hand | Qty to buy | Source | Description | DE | AM | Get | Comment
PB | 1 |  |  | CNC | Peripheral Board Printed Circuit Board |  | 1
PB | 1 |  |  | Mouser | SPST edge mount toggle switch (power) |  |  | 1 | SPDT safer, it’s reversible
PB | 1 |  |  | Mouser | DPDT edge mount toggle switch (5V source) |  |  | 1
PB | 1 |  |  | Mouser | SPST edge mount toggle switch (reset) |  |  | 1 | SPDT safer, it’s reversible
PB | 5 |  |  | Richard | resistors for edge mount LEDs
PB | 5 |  |  | Mouser | edge mount LEDs, various colours
PB | 1 |  |  | Mouser | USB type B edge mount jack
PB | 1 |  |  | DE | 3 pin male header (PB power) |  |  |  | to be separated
PB | 2 |  |  | Richard | step down power regulator |  |  |  | avail at Richards?
PB | 2 |  |  | DE | 4 pin male header (stepper coil wires) | 2 |  |  | to be separated
PB | 1 |  |  | Richard | 4 position DIP switch | 0 |  |  | could use jumpers
 | Qty needed | Qty on hand | Qty to buy | Source | Description | DE | AM | Get | Comment
Other | 2 |  |  | AM? | wheels
Other | 2 |  |  | AM | rubber band wheel tires
Other | 2 |  |  | AM | stepper motors with mounting bolts and washers
Other |  |  |  | ? | parts for battery power harness
Other |  |  |  | DE | parts to put connectors on stepper coil wires
Other |  |  |  | AM | screws for chassis
Other |  |  |  | AM | wood for chassis
Other | 1 |  |  | ? | 4 inch, 25 pin male/male cable between boards
Other | 1 |  |  | AM | battery subassembly
Other | 1 |  |  | AM? | 2 x 16 LCD display with I2C controller

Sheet: Notes
Twipi Part | Supplier | Mfr Part Number | Mouser Part Number | Cost | Details | QTY | Comments
25 pin connector
 | digikey | only has right angle: Amphenol 6E17C-02S-AJ-120-ND
 |  | not sure if footprint is OK
 | mouser canada | seems to have lots | differences may be level of gold plating on contacts
 |  | D25S24A4GV00LF | 649-D25S24A4GV00LF | 4
 |  | KF85X-BD-25S-BR | 806-KF85X-BD-25S-BR | 14.74
 |  | 5745922-2 | 571-5745922-2 | 23.24
 |  | D25S24B6GV00LF | 649-D25S24B6GV00LF | 4.2 |  | 6
 |  | 164A16639X | 706-164A16639X | 14.68
 |  | chart:
 |  | https://www.mouser.ca/Connectors/D-Sub-Connectors/D-Sub-Standard-Connectors/_/N-9gybx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
SPDT | Mouser canada | ET03MD1ABE | 611-ET03-011 | 10.89 |  | 6
DPDT |  | ET23MD1ABE | 611-ET23MD1ABE | 16.08 |  | 3
USB JACK |  | E8144-B02022-L | 673-E8144B02022L | 1.06 |  | 3
LED |  | 5352T1-5VLC | 607-5352T1-5VLC | 4.11 | red
 |  | 5350T1 | 607-5350T1 | 2.93
 |  | SSF-LXH555GD | 696-SSF-LXH555GD | 1.42 | green | 10 | relampable
 |  | SSF-LXH555YD | 696-SSF-LXH555YD | 1.42 | yellow | 10
 |  | SSF-LXH555ID | 696-SSF-LXH555ID | 1.41 | red | 10

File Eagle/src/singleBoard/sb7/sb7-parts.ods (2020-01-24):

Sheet: Parts List
Eagle Part | Eagle Value | Qty | Status | Bin | in bin | Comment
C2 | 100 nF |  | cab | 1B | y | part of battery measurement circuit
C5 | 100 uF ele’lytic |  |  | 1B | y | STEPDRV1 cap on 12V input
C6 | 101 uF ele’lytic |  |  | 1B | y | STEPDRV2 cap on 12V input
C7 | .1 uF |  | cab | 1B | y | ESP32 3.3V decoupling cap
C8 | .1 uF |  | cab | 1B | y | IMU 3.3V decoupling cap
ESP-USB |  |  | await | 1D |  | 4 pin header for ESP32’s console cable | header
FET | IRFD9120 | 3 | cab | 1E | y | battery measurement control FET
GND |  |  |  | 1D |  | 1 pin header for attaching scopes, meters, etc | header
9o |  |  |  | 1D |  | 4 pin header for cable to LCD | header
MS2 | F’Wing_nohols | 2 | cab-c | 2A | y | Adafruit ESP32 Huzzah Featherwing dev’t board | stacking?
R1 | 2K2 | 2 | cab | 2B | y | IMU I2C SCL pullup 2.2K to 3.3V
R2 | 2K2 | 2 | cab | 2B | y | IMU I2C SDA pullup 2.2K to 3.3V
R3 | 4K7 | 2 | cab | 2B | y | LCD I2C SCL pullup 4.7K to 5.0V
R4 | 4K7 | 2 | cab | 2B | y | LCD I2C SDA pullup 4.7K to 5.0V
R5 | now 2K2 |  | cab | 2B | y | top part of battery measurement voltage divider
R6 | 10K | 2 | cab | 2B | y | scaler for 12V indicator LED
R11 | now 270 | 2 | cab | 2C | y | bottom part of battery measurem’t voltage divider
R12 | 100K | 2 | cab | 2C | y | pulldown on battery pwr fed into MOSFET’s gate
STEPDRV1 | POLOL... | 2 | cab | 2D | y | Stepper motor driver #1 DRV8825
aa | ...ULU2128 | 2 | cab | 2D | y | Stepper motor driver #2 DRV8825
SV2 |  |  |  | 1D |  | 4 pin 3 Amp stepper coil header for STEPDRV2 | header
SV3 |  |  |  | 1D |  | 4 pin 3 Amp stepper coil header for STEPDRV1 | header
U1 | GY-521mpu6050 | 2 | cab | 2E | y | IMU
 |  |  |  |  |  | multi-Power regulator for battery to 12V & 5 V
 |  |  |  | 3C | y | ESP32 console to 4 pin header cable | need ends
 |  |  |  |  |  | Pushbutton/LED/USB Jack subassembly (PLUJ)
 |  |  |  | 5A |  | cable from battery to PCB 2 pin keyed header | make
 |  |  |  | 5B |  | stepper coil wiring connectors | build
 |  | 3 | cab | 4A | y | 16 position socket for ESP32
 |  | 3 | cab | 4A | y | 12 position socket for ESP32
 |  | 15 | cab | 4B | y | 8 position socket for IMU, 2 x DRV8825
 |  |  | cab | 3D | y | cable to LCD
 |  | 2 | cab | 4C | y | lighted 3A pushbutton, SPDT, not momentary
 |  | 2 | await | 4D | y | lighted 1A pushbutton - colour1
 |  | 2 | await | 4D | y | lighted 1A pushbutton - colour2
 |  | 2 | await | 4D | y | lighted 1A pushbutton - colour3
 |  | 3 | cab | 4E | y | External USB jack
 |  | 2 |  |  |  | 2 pin jack for battery power, 3A, 25V
 |  |  |  |  |  | 5 pin jack for regulator power, 3A, 25V
 |  |  |  |  |  | 2 conductor battery cable, 3A, 25V
 |  |  |  |  |  | 5 conductor regulator cable, 3A, 25V
Status Codes:
On hand | On Hand, or obtainable from Richard
Ordered | An order has been placed |  |  | cab |  | On hand in the parts cabinet
Yet2Order | Yet to be ordered |  |  | cab-c |  | On hand, with a complication
Build | We need to build it |  |  | await |  | awaiting shipment/delivery

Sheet: Parts Map
Location of components on the parts bin cabinet
1A | 1B | 1C | 1D | 1E
power cable parts | capacitors | 16 pin connectors | headers with pins
2A | 2B | 2C | 2D | 2E
ESP32 | resistors | Pwr monitor parts | stepper drivers | IMU
3A | 3B | 3C | 3D | 3E
24 > 12 V regulator | 12 > 5 V regulator | ESP Console cable
4A | 4B | 4C | 4D | 4E
ESP32 sockets | IMU & DRV sockets | bat PWR switch | non-PWR switches | USB Jack
5A | 5B | 5C | 5D | 5E
16 pin ribbon cable | stepper wire connectors |  |  | USB cable parts
6A | 6B | 6C | 6D | 6E
 |  |  |  |  | 4E

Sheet: Jumpers
NOTES: | -there are no manual jumpers on SB6
 | -there are 3 Vias: one under each DRV8825, and one on ESP32 physical pin 6
 | -to find a component on the board and schematic:
 | -bring up board and schematic in separate windows
 | -in the command line just above the board layout type:
 | sh @ pppp
 | where ppp is the name of the component, like 12V-1 or JP13
 | -note that you can use up arrow to recall last show command

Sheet: Full Schematic Component list
Part | H/W | Jumper | Value | Comment
12V-1 | n | 1W |  | hole for 3 AMP jumper wire to 12V-2
12V-2 | n | 1W |  | hole for 3 AMP jumper wire to 12V-1
12V-3 | n | 2W |  | hole for 3 AMP jumper wire to 12V-4
12V-4 | n | 2W |  | hole for 3 AMP jumper wire to 12V-3
BAT-PWR | y |  |  | 3 pin header to connect battery power
C2 | y |  | ?? | part of battery measurement circuit
C5 | y |  | ?? | STEPDRV1 cap on 12V input
C6 | y |  | ?? | STEPDRV2 cap on 12V input
C7 | y |  | ?? | ESP32 3.3V decoupling cap
C8 | y |  | ?? | IMU 3.3V decoupling cap
CON1 | y |  |  | 16 pin conn’r for pushbuttons, LEDS & USB Jack
D1 | y |  | 1N5400 | protective diode on battery positive
D3 | y |  | 1N5400 | protective diode on battery ground
ESP-USB | y |  |  | 4 pin header for ESP32’s console cable
FET | y |  | IRFD9120 | battery measurement control FET
GND | y |  |  | header for attaching test scopes, meters, etc
JP1 | n | 5 |  | jumper hole to JP2, ESP32 ADC input
JP2 | n | 5 |  | jumper hole to JP1 in battery measurement circuit
JP3 | n | 6 |  | jumper hole to JP4 in battery measurement circuit
JP4 | n | 6 |  | jumper hole to JP3 on battery’s positive side
JP5 | n |  |  | corner of 1st voltage regulator (regulator at end of this list)
JP6 | n |  |  | corner of 1st voltage regulator
JP7 | n |  | OBSOLETE? | corner of 1st voltage regulator
JP8 | n |  | OBSOLETE? | corner of 1st voltage regulator
JP9 | n |  |  | corner of 2nd voltage regulator
JP10 | n |  |  | corner of 2nd voltage regulator
JP11 | n |  |  | corner of 2nd voltage regulator
JP12 | n |  |  | corner of 2nd voltage regulator
JP13 | n | 3W |  | hole for 3 AMP jumper wire to JP14 - LED connector pin 16
JP14 | n | 3W |  | hole for 3 AMP jumper wire to JP13 near big diodes
JP15 | n | 7 |  | jumper hole for STEPDRV1 Sleep pin to JP19
JP16 | n | 7 |  | jumper hole for STEPDRV2 Sleep pin to JP20
JP17 | n | 4W |  | hole for 3 Amp jumper to JP18 - LED connector pin 15
JP18 | n | 4W |  | hole for 3 Amp jumper to JP178 - LED connector pin 16
JP19 | n | 8 |  | jumper hole to STEPDRV1 Sleep pin on JP15
JP20 | n | 8 |  | jumper hole to STEPDRV2 Sleep pin on JP16
LCD-HDR | y |  |  | 4 pin header for cable to LCD
MS2 | y |  | F’Wing_noholes | Adafruit ESP32 Huzzah Featherwing development board
R1 | y |  | 2K2 | IMU I2C SCL pullup 2.2K to 3.3V
R2 | y |  | 2K2 | IMU I2C SDA pullup 2.2K to 3.3V
R3 | y |  | 4K7 | LCD I2C SCL pullup 4.7K to 5.0V
R4 | y |  | 4K7 | LCD I2C SDA pullup 4.7K to 5.0V
R5 | y |  |  | top part of battery measurement voltage divider
R6 | y |  |  | scaler for 12V indicator LED
R11 | y |  |  | bottom part of battery measurement voltage divider
R12 | y |  |  | pulldown on battery power fed into MOSFET’s gate
STEPDRV1 | y |  | POLOLULU2128 | Stepper motor driver #1
STEPDRV2 | y |  | POLOLULU2128 | Stepper motor driver #2
SV2 | y |  |  | 4 pin 3 Amp stepper coil header for STEPDRV2
SV3 | y |  |  | 4 pin 3 Amp stepper coil header for STEPDRV1
U1 | y |  | GY-521MPU6050 | IMU
 | y |  |  | Power regulator for battery to 12V
 | y |  |  | Power regulator for 12V to 5 V
 | y |  |  | ESP32 console to 4 pin header cable
 | y |  |  | Pushbutton/LED/USB Jack subassembly (PLUJ)
 | y |  |  | cable from PLUJ to 16 pin connector on PCB
 | y |  |  | cable from battery to PCB 3 pin header
 | y |  |  | stepper coil wiring connectors
 |  |  |  | SB board
 |  |  |  | note: further manual additions have been made in the parts list sheet

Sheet: PLU Heights
Part Type | Digikey part number | immed. | price | height - mm | height - in
USB Jack | A121598-ND | y | 3.15 | 15.6
 | ED2981-ND
 | 732-2734-ND
 | 151-1083-ND | y | 2.24 | 15.6
 | 5787834-1-ND | y | 3.11 | 15.6
 | SAM10379-ND | y | 2.98 | 15.95
 | 952-1767-ND | y | 1.18 | 16.25
 | GSB422137EU-ND | y | 3.54 | 16.2
 | A121378-ND | y | 4.06 | 15.6
 | 380-1493-ND | y | 1.6 | 16.1
 | SAM10874-ND | y | 3.74 | 15.95
 | 732-8247-ND | y | 2.12 | 16.1
 | 2092-KUSBVX-BS1N-W-ND | y | 1.54 | 16
Switch | 360-3177-ND (5A square .6 in) AMBER | y | 13.69 | 12.5
 | UB16SKG035D-DD-ND amber |  |  | 12.5
 | UB16SKG035F-FF-ND green |  |  | 12.5
 | UB16SKG035C-CC-ND red |  |  | 12.5

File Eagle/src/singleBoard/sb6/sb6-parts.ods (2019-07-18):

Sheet: Parts List
Eagle Part | Eagle Value | Comment | Status | order1 | status | order2 | status | Qty | Bin | digikey
BAT-PWR |  | 2 pin latching header for power fromPLU | On hand |  |  |  | oh | 5 | 1A
C2 | 100 nF | part of battery measurement circuit | On hand |  |  |  |  |  | 1B
C5 | 100 uF electrolytic | STEPDRV1 cap on 12V input | On hand |  |  |  |  |  | 1B
C6 | 100 uF electrolytic | STEPDRV2 cap on 12V input | On hand |  |  |  |  |  | 1B
C7 | .1 uF | ESP32 3.3V decoupling cap | On hand |  |  |  |  |  | 1B
C8 | .1 uF | IMU 3.3V decoupling cap | On hand |  |  |  |  |  | 1B
CON1 |  | 16 pin conn’r for pushbuttons, LEDS & USB Jack | Yet2Order | ‎ED10523-ND‎ (https://www.digikey.ca/product-detail/en/302-S161/ED10523-ND/2794234/?itemSeq=296926024) |  |  | r | 6 | 1C | S9196-ND, S7111-ND, S7076-ND 952-1819-ND, H123831-ND
ESP-USB |  | 4 pin header for ESP32’s console cable | On hand |  |  |  |  |  | 1D
FET | IRFD9120 | battery measurement control FET | Yet2Order | ‎IRFD9120PBF-ND (https://www.digikey.ca/product-detail/en/IRFD9120PBF/IRFD9120PBF-ND/812484/?itemSeq=296926106) |  |  | r | 3 | 1E | IRFD9120PBF-ND
GND |  | 1 pin header for attaching test scopes, meters, etc | On hand |  |  |  |  |  | 1D
LCD-HDR |  | 4 pin header for cable to LCD | On hand |  |  |  |  |  | 1D
MS2 | F’Wing_noholes | Adafruit ESP32 Huzzah Featherwing development board | Yet2Order | ‎1528-2181-ND‎ (https://www.digikey.ca/product-detail/en/3405/1528-2181-ND/7244967/?itemSeq=296926289) |  |  | r | 2 | 2A | 1528-2181-ND
R1 | 2K2 | IMU I2C SCL pullup 2.2K to 3.3V | On hand |  |  |  |  |  | 2B
R2 | 2K2 | IMU I2C SDA pullup 2.2K to 3.3V | On hand |  |  |  |  |  | 2B
R3 | 4K7 | LCD I2C SCL pullup 4.7K to 5.0V | On hand |  |  |  |  |  | 2B
R4 | 4K7 | LCD I2C SDA pullup 4.7K to 5.0V | On hand |  |  |  |  |  | 2B
R5 | 845R 1% | top part of battery measurement voltage divider | On hand |  |  |  |  |  | 2C
R6 | 10K | scaler for 12V indicator LED | On hand |  |  |  |  |  | 2B
R11 | 105R 1% | bottom part of battery measurement voltage divider | On hand |  |  |  |  |  | 2C
R12 | 100K | pulldown on battery power fed into MOSFET’s gate | On hand |  |  |  |  |  | 2C
STEPDRV1 | POLOLULU2128 | Stepper motor driver #1 DRV8825 | Yet2Order |  |  | not ordered | oh |  | 2D | don’t carry it?
STEPDRV2 | POLOLULU2128 | Stepper motor driver #2 DRV8825 | Yet2Order |  |  | not ordered | oh |  | 2D
SV2 |  | 4 pin 3 Amp stepper coil header for STEPDRV2 | On hand |  |  |  |  |  | 1D
SV3 |  | 4 pin 3 Amp stepper coil header for STEPDRV1 | On hand |  |  |  |  |  | 1D
U1 | GY-521MPU6050 | IMU | Yet2Order |  |  | ordered |  | 2 | 2E | don’t carry it?
 |  | Power regulator for battery to 12V | On hand |  |  |  | r |  | 3A
 |  | Power regulator for 12V to 5 V | Yet2Order |  |  |  | r |  | 3B | don’t carry?
 |  | ESP32 console to 4 pin header cable | Build |  |  | ordered |  |  | 3C
 |  | Pushbutton/LED/USB Jack subassembly (PLUJ) | Build
 |  | cable from PLUJ to 16 pin connector on PCB | Yet2Order | ‎3M156034-MC16G-X-6-ND should have been SAM12938-ND (https://www.digikey.ca/product-detail/en/D89116-0131HK-3365%2F16-S-6/3M156034-MC16G-X-6-ND/6024577/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) |  | ordered |  | 3 | 5A | 3M156034-MC16G-X-6-ND 3M156035-MC16G-X-6-ND 3M15390-MC16G-X-6-ND
 |  | cable from battery to PCB 3 pin header | Build |  |  |  |  |  | 5A
 |  | stepper coil wiring connectors | Build |  |  | not ordered |  |  | 5B
 |  | SB4 board | Build
 |  | 16 position socket for ESP32 | Yet2Order | ‎S7014-ND (https://www.digikey.ca/product-detail/en/PPTC161LFBN-RC/S7014-ND/810154/?itemSeq=296928018) |  |  | r | 3 | 4A
 |  | 12 position socket for ESP32 | Yet2Order | ‎1212-1199-ND (https://www.digikey.ca/product-detail/en/801-87-012-10-001101/1212-1199-ND/3757449/?itemSeq=296928879) |  |  | r | 3 | 4A
 |  | 8 position socket for IMU, 2 x DRV8825 | Yet2Order | ‎A106654-ND (https://www.digikey.ca/product-detail/en/215297-8/A106654-ND/2278457/?itemSeq=296938896) |  |  | r | 15 | 4B | A106654-ND
 |  | cable to LCD | On hand
 |  | lighted 3A pushbutton, SPDT, not momentary | Yet2Order | ‎360-3177-ND (https://www.digikey.ca/product-detail/en/UB16SKW035D-JB/360-3177-ND/4512850/?itemSeq=296938967) |  |  | r | 2 | 4C | 360-3177-ND (5A square .6 in) AMBER
 |  | lighted 1A pushbutton - colour1 | Yet2Order | ‎UB16SKG035D-DD-ND‎ (https://www.digikey.ca/product-detail/en/UB16SKG035D-DD/UB16SKG035D-DD-ND/1027349/?itemSeq=296939002) |  |  | bo | 2 | 4D | UB16SKG035D-DD-ND amber
 |  | lighted 1A pushbutton - colour2 | Yet2Order | ‎UB16SKG035F-FF-ND‎ (https://www.digikey.ca/product-detail/en/UB16SKG035F-FF/UB16SKG035F-FF-ND/1027350/?itemSeq=296939015) |  |  | bo | 2 | 4D | UB16SKG035F-FF-ND green
 |  | lighted 1A pushbutton - colour3 | Yet2Order | ‎UB16SKG035C-CC-ND (https://www.digikey.ca/product-detail/en/UB16SKG035C-CC/UB16SKG035C-CC-ND/1027348/?itemSeq=296939055) |  |  | bo | 2 | 4D | UB16SKG035C-CC-ND red
 |  | External USB jack | Yet2Order | ‎A121598-ND‎ (https://www.digikey.ca/product-detail/en/5787834-2/A121598-ND/2286710/?itemSeq=296939125) |  |  | r | 3 | 4E
 |  | 16 position connector for PLUJ board - included in row 8 |  |  |  |  |  |  |  | S5561-ND, S9204-ND, S5522-ND
CON1 |  | 16 pin conn’r for pushbuttons, LEDS & USB Jack RIGHT ANGLE |  |  |  |  |  |  |  | S5561-ND , S9204-ND
 |  | https://www.digikey.ca/product-detail/en/3m/M3UUK-1606R/M3UUK-1606R-ND/233167

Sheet: Parts Map
Location of components on the parts bin cabinet
1A | 1B | 1C | 1D | 1E
power cable parts | capacitors | 16 pin connectors | headers with pins
2A | 2B | 2C | 2D | 2E
ESP32 | resistors | Pwr monitor parts | stepper drivers | IMU
3A | 3B | 3C | 3D | 3E
24 > 12 V regulator | 12 > 5 V regulator | ESP Console cable
4A | 4B | 4C | 4D | 4E
ESP32 sockets | IMU & DRV sockets | bat PWR switch | non-PWR switches | USB Jack
5A | 5B | 5C | 5D | 5E
16 pin ribbon cable | stepper wire connectors |  |  | USB cable parts
6A | 6B | 6C | 6D | 6E
 |  |  |  |  | 4E

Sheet: Jumpers
NOTES: | -there are no manual jumpers on SB6
 | -there are 3 Vias: one under each DRV8825, and one on ESP32 physical pin 6
 | -to find a component on the board and schematic:
 | -bring up board and schematic in separate windows
 | -in the command line just above the board layout type:
 | sh @ pppp
 | where ppp is the name of the component, like 12V-1 or JP13
 | -note that you can use up arrow to recall last show command

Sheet: Full Schematic Component list
Part | H/W | Jumper | Value | Comment
12V-1 | n | 1W |  | hole for 3 AMP jumper wire to 12V-2
12V-2 | n | 1W |  | hole for 3 AMP jumper wire to 12V-1
12V-3 | n | 2W |  | hole for 3 AMP jumper wire to 12V-4
12V-4 | n | 2W |  | hole for 3 AMP jumper wire to 12V-3
BAT-PWR | y |  |  | 3 pin header to connect battery power
C2 | y |  | ?? | part of battery measurement circuit
C5 | y |  | ?? | STEPDRV1 cap on 12V input
C6 | y |  | ?? | STEPDRV2 cap on 12V input
C7 | y |  | ?? | ESP32 3.3V decoupling cap
C8 | y |  | ?? | IMU 3.3V decoupling cap
CON1 | y |  |  | 16 pin conn’r for pushbuttons, LEDS & USB Jack
D1 | y |  | 1N5400 | protective diode on battery positive
D3 | y |  | 1N5400 | protective diode on battery ground
ESP-USB | y |  |  | 4 pin header for ESP32’s console cable
FET | y |  | IRFD9120 | battery measurement control FET
GND | y |  |  | header for attaching test scopes, meters, etc
JP1 | n | 5 |  | jumper hole to JP2, ESP32 ADC input
JP2 | n | 5 |  | jumper hole to JP1 in battery measurement circuit
JP3 | n | 6 |  | jumper hole to JP4 in battery measurement circuit
JP4 | n | 6 |  | jumper hole to JP3 on battery’s positive side
JP5 | n |  |  | corner of 1st voltage regulator (regulator at end of this list)
JP6 | n |  |  | corner of 1st voltage regulator
JP7 | n |  | OBSOLETE? | corner of 1st voltage regulator
JP8 | n |  | OBSOLETE? | corner of 1st voltage regulator
JP9 | n |  |  | corner of 2nd voltage regulator
JP10 | n |  |  | corner of 2nd voltage regulator
JP11 | n |  |  | corner of 2nd voltage regulator
JP12 | n |  |  | corner of 2nd voltage regulator
JP13 | n | 3W |  | hole for 3 AMP jumper wire to JP14 - LED connector pin 16
JP14 | n | 3W |  | hole for 3 AMP jumper wire to JP13 near big diodes
JP15 | n | 7 |  | jumper hole for STEPDRV1 Sleep pin to JP19
JP16 | n | 7 |  | jumper hole for STEPDRV2 Sleep pin to JP20
JP17 | n | 4W |  | hole for 3 Amp jumper to JP18 - LED connector pin 15
JP18 | n | 4W |  | hole for 3 Amp jumper to JP178 - LED connector pin 16
JP19 | n | 8 |  | jumper hole to STEPDRV1 Sleep pin on JP15
JP20 | n | 8 |  | jumper hole to STEPDRV2 Sleep pin on JP16
LCD-HDR | y |  |  | 4 pin header for cable to LCD
MS2 | y |  | F’Wing_noholes | Adafruit ESP32 Huzzah Featherwing development board
R1 | y |  | 2K2 | IMU I2C SCL pullup 2.2K to 3.3V
R2 | y |  | 2K2 | IMU I2C SDA pullup 2.2K to 3.3V
R3 | y |  | 4K7 | LCD I2C SCL pullup 4.7K to 5.0V
R4 | y |  | 4K7 | LCD I2C SDA pullup 4.7K to 5.0V
R5 | y |  |  | top part of battery measurement voltage divider
R6 | y |  |  | scaler for 12V indicator LED
R11 | y |  |  | bottom part of battery measurement voltage divider
R12 | y |  |  | pulldown on battery power fed into MOSFET’s gate
STEPDRV1 | y |  | POLOLULU2128 | Stepper motor driver #1
STEPDRV2 | y |  | POLOLULU2128 | Stepper motor driver #2
SV2 | y |  |  | 4 pin 3 Amp stepper coil header for STEPDRV2
SV3 | y |  |  | 4 pin 3 Amp stepper coil header for STEPDRV1
U1 | y |  | GY-521MPU6050 | IMU
 | y |  |  | Power regulator for battery to 12V
 | y |  |  | Power regulator for 12V to 5 V
 | y |  |  | ESP32 console to 4 pin header cable
 | y |  |  | Pushbutton/LED/USB Jack subassembly (PLUJ)
 | y |  |  | cable from PLUJ to 16 pin connector on PCB
 | y |  |  | cable from battery to PCB 3 pin header
 | y |  |  | stepper coil wiring connectors
 |  |  |  | SB board
 |  |  |  | note: further manual additions have been made in the parts list sheet

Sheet: PLU Heights
Part Type | Digikey part number | immed. | price | height - mm | height - in
USB Jack | A121598-ND | y | 3.15 | 15.6
 | ED2981-ND
 | 732-2734-ND
 | 151-1083-ND | y | 2.24 | 15.6
 | 5787834-1-ND | y | 3.11 | 15.6
 | SAM10379-ND | y | 2.98 | 15.95
 | 952-1767-ND | y | 1.18 | 16.25
 | GSB422137EU-ND | y | 3.54 | 16.2
 | A121378-ND | y | 4.06 | 15.6
 | 380-1493-ND | y | 1.6 | 16.1
 | SAM10874-ND | y | 3.74 | 15.95
 | 732-8247-ND | y | 2.12 | 16.1
 | 2092-KUSBVX-BS1N-W-ND | y | 1.54 | 16
Switch | 360-3177-ND (5A square .6 in) AMBER | y | 13.69 | 12.5
 | UB16SKG035D-DD-ND amber |  |  | 12.5
 | UB16SKG035F-FF-ND green |  |  | 12.5
 | UB16SKG035C-CC-ND red |  |  | 12.5

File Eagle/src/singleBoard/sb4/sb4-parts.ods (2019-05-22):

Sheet: Parts List
Eagle Part | Eagle Value | Comment | Status | digikey | Mouser
BAT-PWR |  | 3 pin header to connect battery power | On hand
C2 | 100 nF | part of battery measurement circuit | On hand
C5 | 100 uF electrolytic | STEPDRV1 cap on 12V input | On hand
C6 | 100 uF electrolytic | STEPDRV2 cap on 12V input | On hand
C7 | .1 uF | ESP32 3.3V decoupling cap | On hand
C8 | .1 uF | IMU 3.3V decoupling cap | On hand
CON1 |  | 16 pin conn’r for pushbuttons, LEDS & USB Jack | Yet2Order | S9196-ND, S7111-ND, S7076-ND 952-1819-ND, H123831-ND
D1 | 1N5400 | protective diode on battery positive | On hand
D3 | 1N5400 | protective diode on battery ground | On hand
ESP-USB |  | 4 pin header for ESP32’s console cable | On hand
FET | IRFD9120 | battery measurement control FET | Yet2Order | IRFD9120PBF-ND
GND |  | 1 pin header for attaching test scopes, meters, etc | On hand
LCD-HDR |  | 4 pin header for cable to LCD | On hand
MS2 | F’Wing_noholes | Adafruit ESP32 Huzzah Featherwing development board | Yet2Order | 1528-2181-ND
R1 | 2K2 | IMU I2C SCL pullup 2.2K to 3.3V | On hand
R2 | 2K2 | IMU I2C SDA pullup 2.2K to 3.3V | On hand
R3 | 4K7 | LCD I2C SCL pullup 4.7K to 5.0V | On hand
R4 | 4K7 | LCD I2C SDA pullup 4.7K to 5.0V | On hand
R5 | 845R 1% | top part of battery measurement voltage divider | On hand
R6 | 10K | scaler for 12V indicator LED | On hand
R11 | 105R 1% | bottom part of battery measurement voltage divider | On hand
R12 | 100K | pulldown on battery power fed into MOSFET’s gate | On hand
STEPDRV1 | POLOLULU2128 | Stepper motor driver #1 DRV8825 | Yet2Order | don’t carry it?
STEPDRV2 | POLOLULU2128 | Stepper motor driver #2 DRV8825 | Yet2Order
SV2 |  | 4 pin 3 Amp stepper coil header for STEPDRV2 | On hand
SV3 |  | 4 pin 3 Amp stepper coil header for STEPDRV1 | On hand
U1 | GY-521MPU6050 | IMU | Yet2Order | don’t carry it?
 |  | Power regulator for battery to 12V | Ordered
 |  | Power regulator for 12V to 5 V | Yet2Order | don’t carry?
 |  | ESP32 console to 4 pin header cable | Build
 |  | Pushbutton/LED/USB Jack subassembly (PLUJ) | Build
 |  | cable from PLUJ to 16 pin connector on PCB | Yet2Order | 3M156034-MC16G-X-6-ND 3M156035-MC16G-X-6-ND 3M15390-MC16G-X-6-ND | 6 inch, keyed, female 6 inch, keyed, female 6 inch, keyed, female
 |  | cable from battery to PCB 3 pin header | Build
 |  | stepper coil wiring connectors | Build
 |  | SB4 board | Build
 |  | sockets for ESP32 | Yet2Order
 |  | socket for IMU | On hand
 |  | socket for DRV8825 | On hand
 |  | cable to LCD | On hand
 |  | lighted 3A pushbutton, SPDT, not momentary | Yet2Order | 360-3177-ND (5A square .6 in) | 612-ULV7F2BSS351
 |  | lighted 1A pushbutton - colour1 | Yet2Order | separate LEDs ?
 |  | lighted 1A pushbutton - colour2 | Yet2Order
 |  | lighted 1A pushbutton - colour3 | Yet2Order
 |  | External USB jack | Yet2Order
 |  | 16 position connector for PLUJ board |  | S5561-ND, S9204-ND, S5522-ND
Status Codes:
 | On hand | On Hand, or obtainable from Richard
 | Ordered | An order has been placed
 | Yet2Order | Yet to be ordered
 | Build | We need to build it
CON1 |  | 16 pin conn’r for pushbuttons, LEDS & USB Jack RIGHT ANGLE | Yet2Order | S5561-ND , S9204-ND
 |  | https://www.digikey.ca/product-detail/en/3m/M3UUK-1606R/M3UUK-1606R-ND/233167

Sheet: Jumpers
Part | H/W | Jumper | Value | Comment
12V-1 | n | 1W |  | hole for 3 AMP jumper wire to 12V-2
12V-2 | n | 1W |  | hole for 3 AMP jumper wire to 12V-1
12V-3 | n | 2W |  | hole for 3 AMP jumper wire to 12V-4
12V-4 | n | 2W |  | hole for 3 AMP jumper wire to 12V-3
JP1 | n | 5 |  | jumper hole to JP2, ESP32 ADC input
JP2 | n | 5 |  | jumper hole to JP1 in battery measurement circuit
JP3 | n | 6 |  | jumper hole to JP4 in battery measurement circuit
JP4 | n | 6 |  | jumper hole to JP3 on battery’s positive side
JP13 | n | 3W |  | hole for 3 AMP jumper wire to JP14 - LED connector pin 16
JP14 | n | 3W |  | hole for 3 AMP jumper wire to JP13 near big diodes
JP15 | n | 7 |  | jumper hole for STEPDRV1 Sleep pin to JP19
JP16 | n | 7 |  | jumper hole for STEPDRV2 Sleep pin to JP20
JP17 | n | 4W |  | hole for 3 Amp jumper to JP18 - LED connector pin 15
JP18 | n | 4W |  | hole for 3 Amp jumper to JP178 - LED connector pin 16
JP19 | n | 8 |  | jumper hole to STEPDRV1 Sleep pin on JP15
JP20 | n | 8 |  | jumper hole to STEPDRV2 Sleep pin on JP16
 |  |  | NOTES: | -there are 8 jumpers. Both ends of each one is listed above
 |  |  |  | -jumper ID's that end in W are thicker to accommodate 3 Amps.
 |  |  |  | -to find a component on the board and schematic:
 |  |  |  | -bring up board and schematic in separate windows
 |  |  |  | -in the command line just above the board layout type:
 |  |  |  | sh @ pppp
 |  |  |  | where ppp is the name of the component, like 12V-1 or JP13
 |  |  |  | -note that you can use up arrow to recall last show command

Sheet: Full Schematic Component list
Part | H/W | Jumper | Value | Comment
12V-1 | n | 1W |  | hole for 3 AMP jumper wire to 12V-2
12V-2 | n | 1W |  | hole for 3 AMP jumper wire to 12V-1
12V-3 | n | 2W |  | hole for 3 AMP jumper wire to 12V-4
12V-4 | n | 2W |  | hole for 3 AMP jumper wire to 12V-3
BAT-PWR | y |  |  | 3 pin header to connect battery power
C2 | y |  | ?? | part of battery measurement circuit
C5 | y |  | ?? | STEPDRV1 cap on 12V input
C6 | y |  | ?? | STEPDRV2 cap on 12V input
C7 | y |  | ?? | ESP32 3.3V decoupling cap
C8 | y |  | ?? | IMU 3.3V decoupling cap
CON1 | y |  |  | 16 pin conn’r for pushbuttons, LEDS & USB Jack
D1 | y |  | 1N5400 | protective diode on battery positive
D3 | y |  | 1N5400 | protective diode on battery ground
ESP-USB | y |  |  | 4 pin header for ESP32’s console cable
FET | y |  | IRFD9120 | battery measurement control FET
GND | y |  |  | header for attaching test scopes, meters, etc
JP1 | n | 5 |  | jumper hole to JP2, ESP32 ADC input
JP2 | n | 5 |  | jumper hole to JP1 in battery measurement circuit
JP3 | n | 6 |  | jumper hole to JP4 in battery measurement circuit
JP4 | n | 6 |  | jumper hole to JP3 on battery’s positive side
JP5 | n |  |  | corner of 1st voltage regulator (regulator at end of this list)
JP6 | n |  |  | corner of 1st voltage regulator
JP7 | n |  | OBSOLETE? | corner of 1st voltage regulator
JP8 | n |  | OBSOLETE? | corner of 1st voltage regulator
JP9 | n |  |  | corner of 2nd voltage regulator
JP10 | n |  |  | corner of 2nd voltage regulator
JP11 | n |  |  | corner of 2nd voltage regulator
JP12 | n |  |  | corner of 2nd voltage regulator
JP13 | n | 3W |  | hole for 3 AMP jumper wire to JP14 - LED connector pin 16
JP14 | n | 3W |  | hole for 3 AMP jumper wire to JP13 near big diodes
JP15 | n | 7 |  | jumper hole for STEPDRV1 Sleep pin to JP19
JP16 | n | 7 |  | jumper hole for STEPDRV2 Sleep pin to JP20
JP17 | n | 4W |  | hole for 3 Amp jumper to JP18 - LED connector pin 15
JP18 | n | 4W |  | hole for 3 Amp jumper to JP178 - LED connector pin 16
JP19 | n | 8 |  | jumper hole to STEPDRV1 Sleep pin on JP15
JP20 | n | 8 |  | jumper hole to STEPDRV2 Sleep pin on JP16
LCD-HDR | y |  |  | 4 pin header for cable to LCD
MS2 | y |  | F’Wing_noholes | Adafruit ESP32 Huzzah Featherwing development board
R1 | y |  | 2K2 | IMU I2C SCL pullup 2.2K to 3.3V
R2 | y |  | 2K2 | IMU I2C SDA pullup 2.2K to 3.3V
R3 | y |  | 4K7 | LCD I2C SCL pullup 4.7K to 5.0V
R4 | y |  | 4K7 | LCD I2C SDA pullup 4.7K to 5.0V
R5 | y |  |  | top part of battery measurement voltage divider
R6 | y |  |  | scaler for 12V indicator LED
R11 | y |  |  | bottom part of battery measurement voltage divider
R12 | y |  |  | pulldown on battery power fed into MOSFET’s gate
STEPDRV1 | y |  | POLOLULU2128 | Stepper motor driver #1
STEPDRV2 | y |  | POLOLULU2128 | Stepper motor driver #2
SV2 | y |  |  | 4 pin 3 Amp stepper coil header for STEPDRV2
SV3 | y |  |  | 4 pin 3 Amp stepper coil header for STEPDRV1
U1 | y |  | GY-521MPU6050 | IMU
 | y |  |  | Power regulator for battery to 12V
 | y |  |  | Power regulator for 12V to 5 V
 | y |  |  | ESP32 console to 4 pin header cable
 | y |  |  | Pushbutton/LED/USB Jack subassembly (PLUJ)
 | y |  |  | cable from PLUJ to 16 pin connector on PCB
 | y |  |  | cable from battery to PCB 3 pin header
 | y |  |  | stepper coil wiring connectors
 |  |  |  | SB board
 |  |  |  | note: further manual additions have been made in the parts list sheet

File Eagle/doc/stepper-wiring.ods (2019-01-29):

DRV8825, Component Side |  |  | A4988, Component Side
ENA | VMOT |  | ENA | VMOT
M0 | GND |  | MS1 | GND
M1 | B2 |  | MS2 | 2B
M2 | B1 |  | MS3 | 2A
_RESET | A1 |  | _RESET | 1A
_SLEEP | A2 |  | _SLEEP | 1B
STEP | _FAULT |  | STEP | VDD
DIR | GND |  | DIR | GND
For DRV8825 stepper leads, |  |  | For A4988 stepper leads,
A & B are coil identifiers |  |  | 1 and 2 are coil identifiers
Stepper Motor Wiring Connection |  |  | NOTE: Headers have different pinouts
Motor on Robot’s Right
Pin on header | Interboard pin number | DRV8825 stepper lead | DRV8825 pin number | Stepper wire colour
P1 | 19 | A2 | 11 | black
P2 | 18 | A1 | 12 | green
P3 | 17 | B1 | 13 | red
P4 | 16 | B2 | 14 | blue
Motor on Robot’s Left
Pin on header | Interboard pin number | DRV8825 stepper lead | DRV8825 pin number | Stepper wire colour
P4 | 4 | B2 | 14 | blue
P3 | 3 | B1 | 13 | red
P2 | 2 | A1 | 12 | black
P1 | 1 | A2 | 11 | green
 |  | Peripheral Board

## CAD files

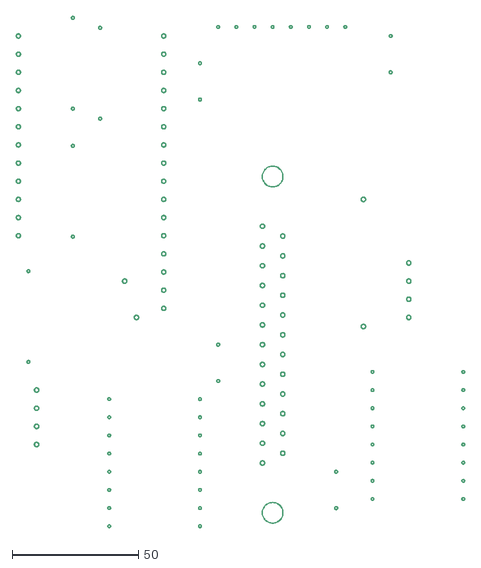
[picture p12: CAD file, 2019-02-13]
Eagle/src/mainBoard/Gcode/test7/drills.dxf
177.8 x 202.7

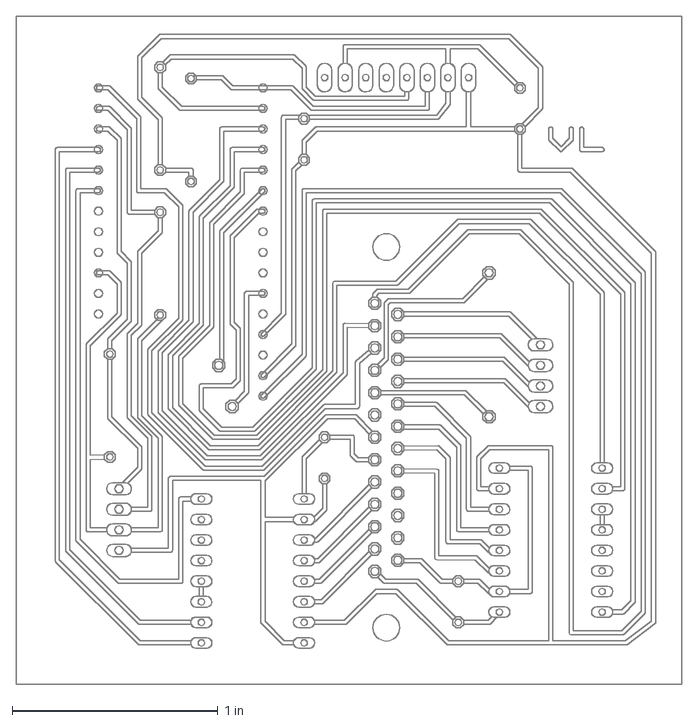
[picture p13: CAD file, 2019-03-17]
Eagle/src/mainBoard/Gcode/test8/CAMOutputs/DrawingFiles/twip-mb2.dxf
3.24 x 3.25 in

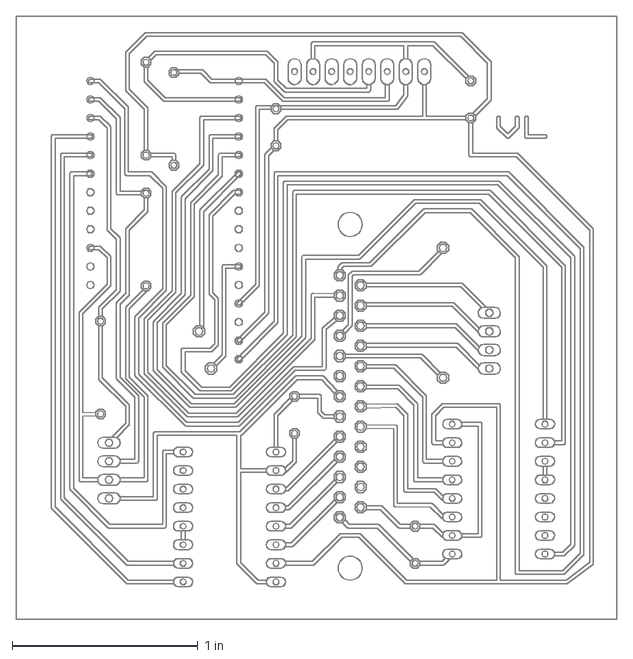
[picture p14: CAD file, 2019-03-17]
Eagle/src/mainBoard/Gcode/test9/CAMOutputs/DrawingFiles/twip-mb2.dxf
3.24 x 3.25 in

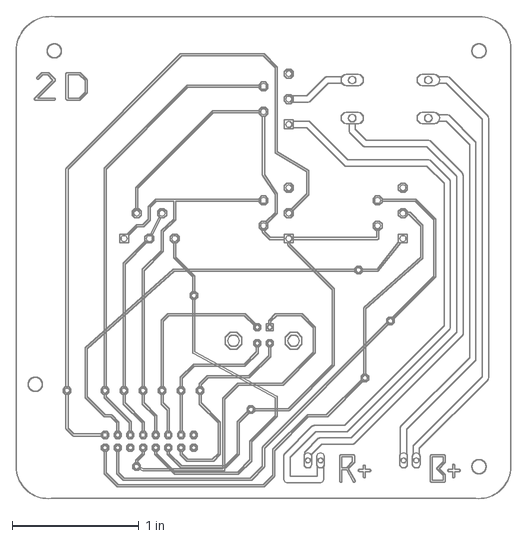
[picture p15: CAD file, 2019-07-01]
Eagle/src/singleBoard/pl2/CAMOutputs/DrawingFiles/plu.dxf
3.90 x 3.80 in

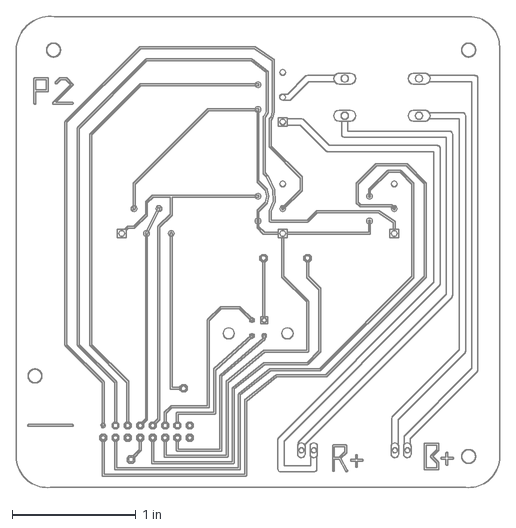
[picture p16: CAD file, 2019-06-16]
Eagle/src/singleBoard/plu/CAMOutputs/DrawingFiles/plu.dxf
3.90 x 3.80 in

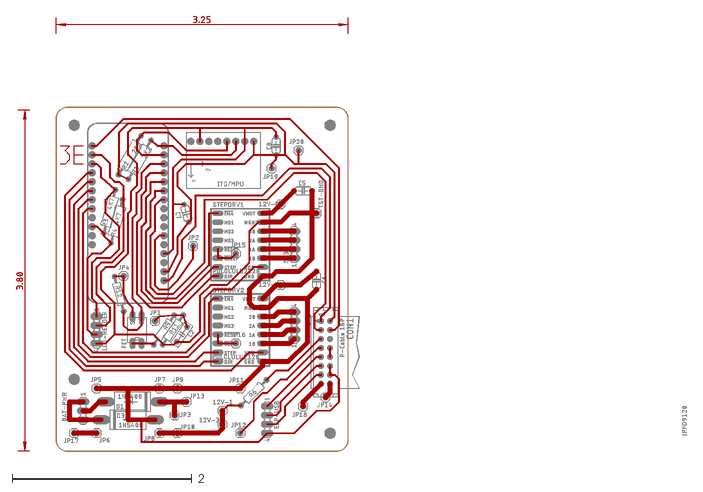
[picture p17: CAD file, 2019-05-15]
Eagle/src/singleBoard/sb3/sb3.dxf
7.46 x 4.85

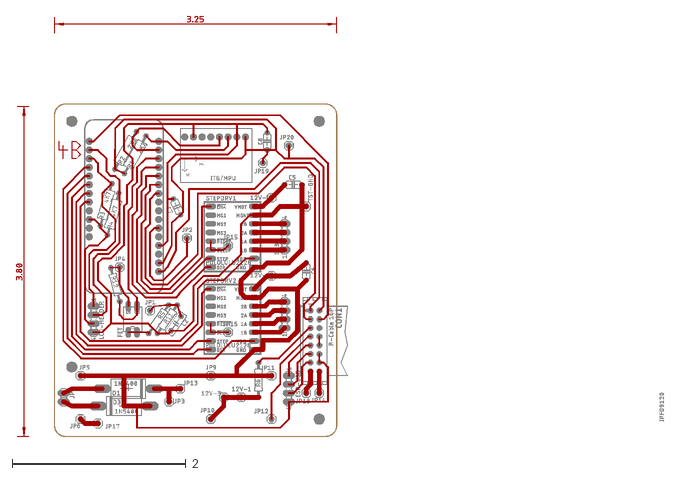
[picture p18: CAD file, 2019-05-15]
Eagle/src/singleBoard/sb4/sb4.dxf
7.46 x 4.85

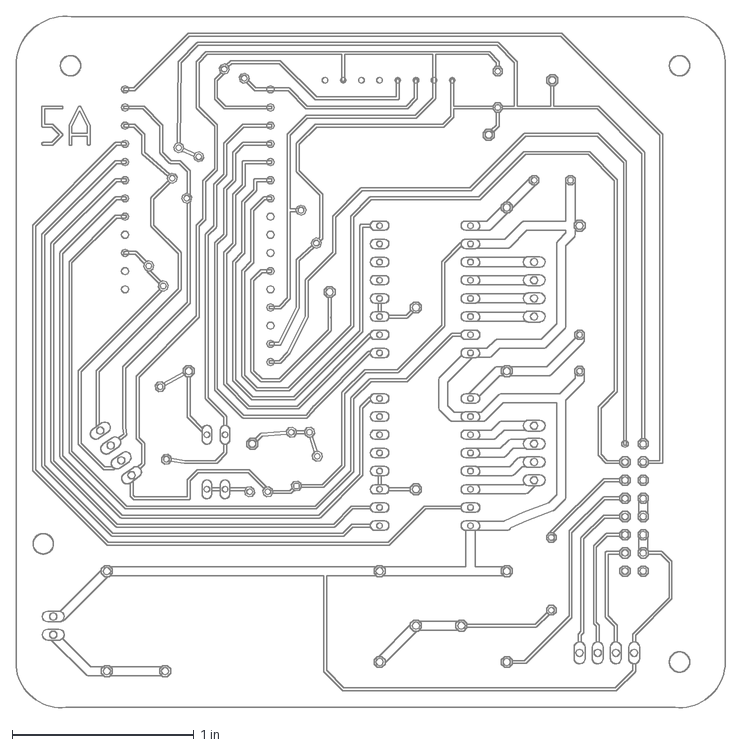
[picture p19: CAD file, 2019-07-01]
Eagle/src/singleBoard/sb5/CAMOutputs/DrawingFiles/sb5-nofix.dxf
3.90 x 3.80 in

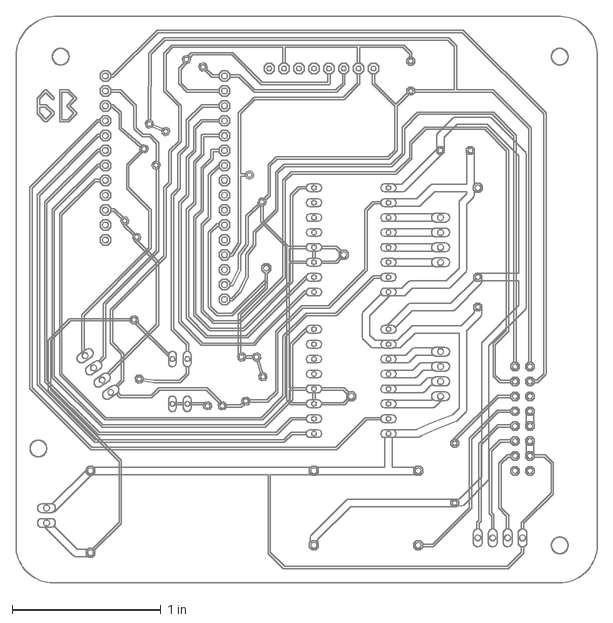
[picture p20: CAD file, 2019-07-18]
Eagle/src/singleBoard/sb6/CAMOutputs/DrawingFiles/sb6pads.dxf
3.90 x 3.80 in

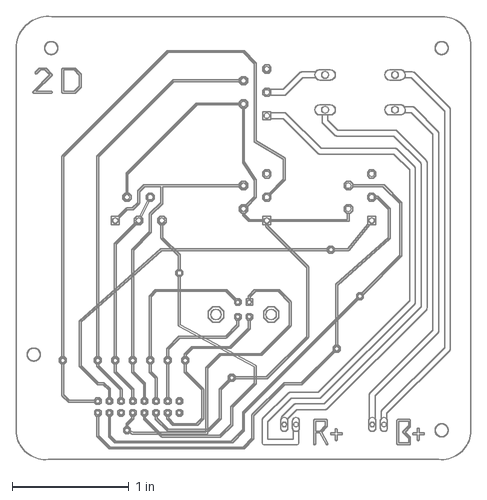
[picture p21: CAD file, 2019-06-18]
Eagle/src/singleBoard/pl2/CAMOutputs/DrawingFiles/plu-rel2d.dxf
3.90 x 3.80 in

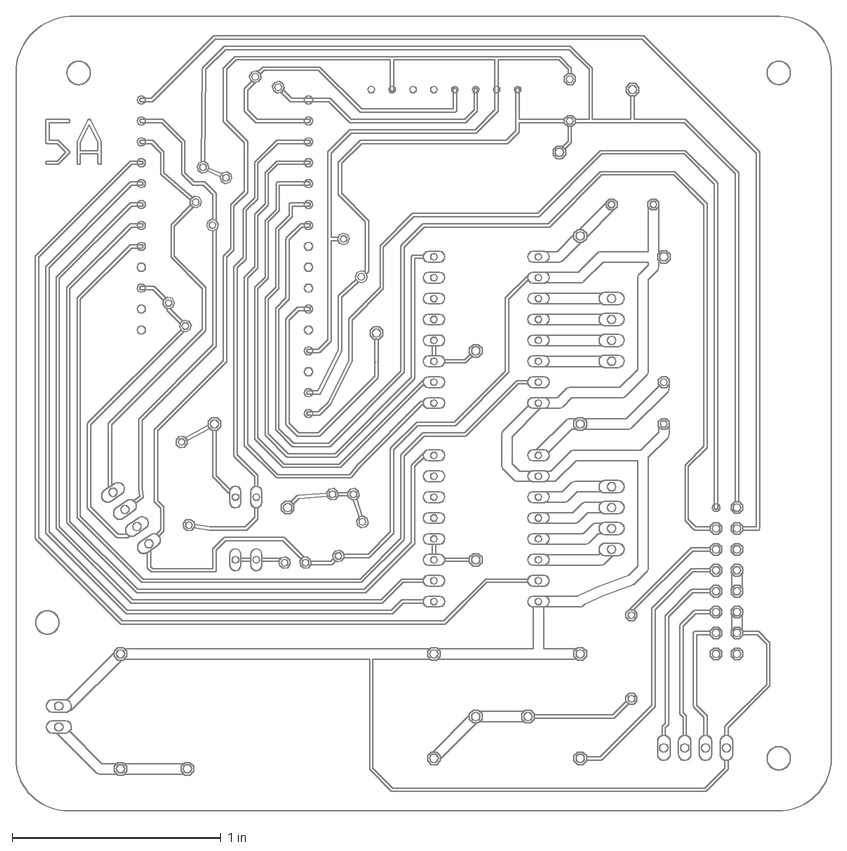
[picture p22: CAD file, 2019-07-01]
Eagle/src/singleBoard/sb5/CAMOutputs/DrawingFiles/sb5.dxf
3.90 x 3.80 in

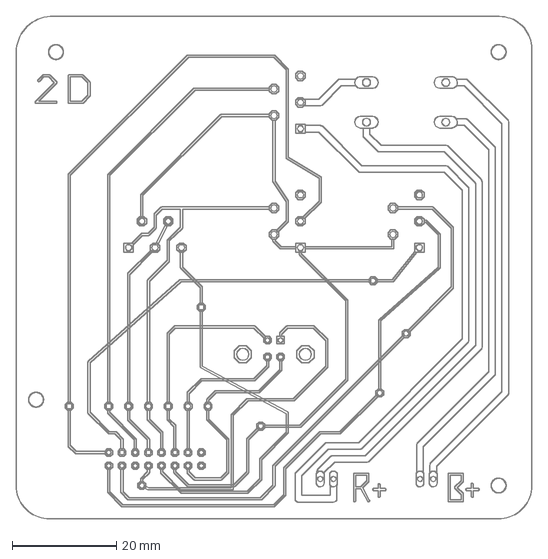
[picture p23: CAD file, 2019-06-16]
Eagle/src/singleBoard/pl2/CAMOutputs/DrawingFiles/plu-first.dxf
99.1 x 96.6 mm

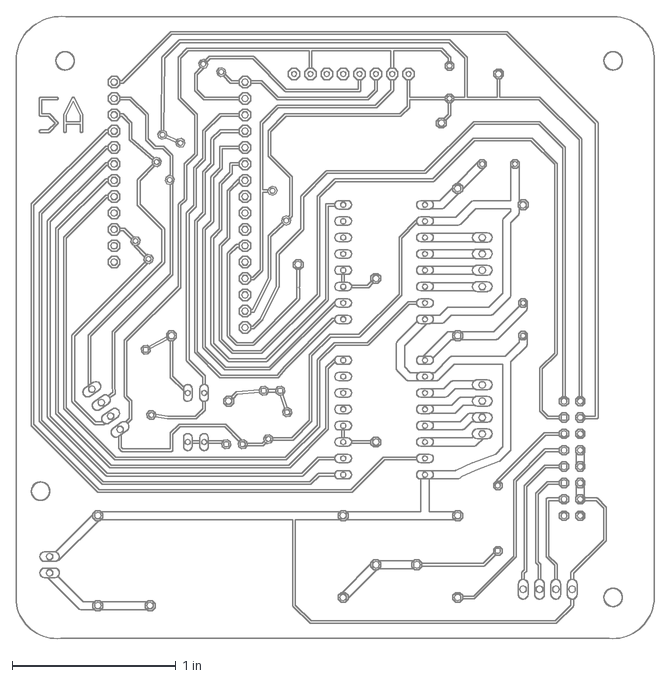
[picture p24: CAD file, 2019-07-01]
Eagle/src/singleBoard/sb5/CAMOutputs/DrawingFiles/t.dxf
3.90 x 3.80 in

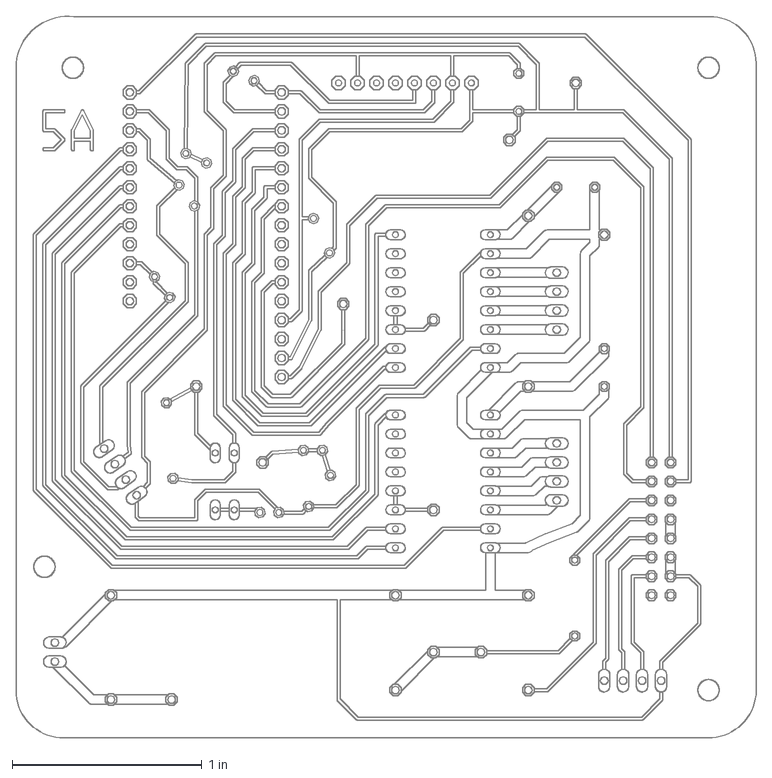
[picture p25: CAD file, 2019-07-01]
Eagle/src/singleBoard/sb5/CAMOutputs/DrawingFiles/sb5a.dxf
3.90 x 3.80 in

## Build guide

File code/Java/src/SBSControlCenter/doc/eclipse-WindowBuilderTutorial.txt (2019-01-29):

Create a new WindowBuilder Java application in Eclipse
Instructions from: https://examples.javacodegeeks.com/desktop-java/ide/eclipse/eclipse-window-builder-tutorial-gui-creation/
Steps:
1. Create new project
- Click on File=>New=>Other
- Browse to WindowBuilder=>SWT Designer and choose SWT/JFace Java Project. Click Next.
- In the ‘Project name:’ text box give the project name. We will use WindowBuilderProject. Leave the other options as default and click Finish.

2. Create new SWT (Standard Widget Toolkit) application
- Click on File=>New=>Other
- Browse to WindowBuilder=>SWT Designer=>SWT and choose ‘Application Window’ 
- Click Next
- Enter the Name and select the project created in step 1
- Click on Finish

3. Go into design View
- Click on the class you just created
- Click the Design View tab

Add graphing capabilities to Java using JFreechart
Instructions from: http://www.codejava.net/java-se/graphics/using-jfreechart-to-draw-xy-line-chart-with-xydataset

1. To use JFreechart in your project, add the following JAR files to the project’s classpath
- Create lib directory in your project
- Copy over these files
    jcommon-VERSION.jar
    jfreechart-VERSION.jar
- In Eclipse, left click on the project name=>Build Path=>Add External archives
- Select both jar filesAdd charts

Creating JFreechart classes
1. This is a very good link for embedding JFreechart into a Java GUI using WindowBuilder: http://junaedhalim.blogspot.ca/2009/12/how-to-embed-jfreechart-in-jpanel.html

JSON parse name/value pair formatted message
		// Create data set to be used by chart
		DefaultPieDataset result = new DefaultPieDataset();               
        result.setValue("Linux", 29);
        result.setValue("Mac", 20);
        result.setValue("Windows", 51);

        // Define JFreechart look 
        JFreeChart chart = ChartFactory.createPieChart3D
        (
            "Pie Chart",           // chart title
            result,                // data
            true,                  // include legend
            true,                  // ??
            false                  // ??
        );

JSON parse array formatted message       
        // Quick parse of JSON array message
        JSONParser parser = new JSONParser();
        String s = "[0,{\"1\":{\"2\":{\"3\":{\"4\":[5,{\"6\":7}]}}}}]";  		
        try
        {
           Object objIN = parser.parse(s);
           JSONArray array = (JSONArray)objIN;
  			
           System.out.println("The 2nd element of array");
           System.out.println(array.get(1));
           System.out.println();

           JSONObject obj2 = (JSONObject)array.get(1);
           System.out.println("Field \"1\"");
           System.out.println(obj2.get("1"));    

           s = "{}";
           objIN = parser.parse(s);
           System.out.println(objIN);

           s = "[5,]";
           objIN = parser.parse(s);
           System.out.println(objIN);

           s = "[5,,2]";
           objIN = parser.parse(s);
           System.out.println(objIN);
        }
        catch(ParseException pe)
        {
  		
           System.out.println("position: " + pe.getPosition());
           System.out.println(pe);
        }

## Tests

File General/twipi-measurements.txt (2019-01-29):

using robots left wheel,

step goes to gpio 32, pin 20
  step is beside dir, one pin in from end of line
dir goes to gpio 14, pin 19
  dir is pin on side where pot is, on opposite end of the line

sleep and reset are next to dir

On DRV825
dir

robot measurements
 weight = approximately 4 pounds, 1.8 Kg
 height = 10 inches
 axle height = 2 inches 
 mass distribution: 6.5 inches above axle
 
assume a max travel speed of 12 inches / second

------------

if he's at 5 degree tilt, what torque is needed to

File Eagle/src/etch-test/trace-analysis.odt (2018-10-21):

Examination of Etch Widths In Eagle > FlatCAM > G-CodeFiles

Test files:

etch-fun.sch, etch-fun.brd

-Eagle files for minimal circuiit to simplify analysis

tst1-trace-by-wiki.nc, tst1-drill-by-wiki.nc

-G-Code files produced from etch-fun files by following procedure and parameter settings in our wiki.

- parameter settings are documented in the cad-conversions.ods file as well

chart-data.ods

- import of trace file G-Code corners into a spreadsheet

- charted using a scatter graph to allow examination of data points from the shapes

The bottom right corner of the circuit has a trace running between the larger of the pads which seems like a good case to examine. The scatter graph for that part looks like this:


The cross section of the vertical trace looks like this:


Adding the 0.009 inch width of the V bit to the diagram, we get:


In this case, we could double the trace width to .012 inches in EagleCAD and there would be enough room between the pads. There would be a .005 space between the pads and the edge of the toolpath. This change seems to work through EagleCAD, and FlatCAM, and produces the expected G-Codes.

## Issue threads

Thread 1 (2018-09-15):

[E][esp32-hal-i2c.c:1146] i2cCheckLineState(): Bus Invalid State, TwoWire() Can't init

va3wam, 2018-09-15:
main.ino throws the exception [E][esp32-hal-i2c.c:1146] i2cCheckLineState(): Bus Invalid State, TwoWire() Can't init. The "initialization complete" message shows up in the terminal trace with only a few of these errors appearing. Once the timer is set the error floods the terminal trace. The last message received on the LCD is "Boot Sequence" on line 1 and "Start Websockets" on line 2. This seems to be consistent across reboots of the Huzzah32.

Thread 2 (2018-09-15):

Build PCB(s)

va3wam, 2018-09-15:
Get a new circuit boards built and tested and installed into TWIPi.

nerdoug, 2018-09-19:
To Do's:
-decide on board orientation and position
-decide which side of MB the IBC connector should be mounted
    -may require MB notch to allow IBC cable to reach PB
-decide how we implement card cage "rails"
    -slots cut into existing pieces on all 4 sides, or 3 sides
    -built up edge holders as part of 4 vertical panels, on 3 or 4 sides
    -4 sides approach lets boards come out through any side
-get PB1A and PB1B layouts done, with associated ICB pinout changes

Closed 2018-09-19.

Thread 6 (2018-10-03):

Create shopping list of parts

va3wam, 2018-10-03:
Need to get a list of parts to stuff the PCB boards that we are making.

va3wam, 2018-10-17:
See issues 7 and 10 for details needed to purchase the correct motors. Also see task 11 regarding purchasing the items from this list.

nerdoug, 2018-10-19:
initial parts list uploaded to /.../EagleCAD/doc . More details and part numbers needed, and the results of some ongoing investigations.

Closed 2018-10-19.

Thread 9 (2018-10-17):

Build main and peripheral PCBs

va3wam, 2018-10-17:
Successfully mill and populate the two boards designed by Doug

va3wam, 2018-10-23:
Notes from Doug’s email. Test run with 2/3 successful traces was from file t4-tr-d005.nc, in
our programs/Doug/pcb-stuff folder on 770. Two of 3 traces has conductivity, and we're hoping that using a 10 degree taper bit will generate more robust traces.

Next steps:
-manually set x, y, and z, and run same job with new 10 degree bit.
-for drill file, use t4-dr-d003.nc

Option 2
Another avenue to pursue: Tell Eagle CAD that we're using a bigger bit, so it lays out the traces with wider center lines on the isolating channels.

Settings:
These files have settings that were used:
f = 9.0 /feed
spindle speed = 5000
Z depth for traces was -.005

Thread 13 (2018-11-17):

Wiring updates needed for next iteration of PCBs

va3wam, 2018-11-17:
1. Use female headers not male headers so it is easy to breadboard components for testing
2. Move jumpers for motors away from 25 pin connector for better cable clearance. In fact, maximize clearance around headers in general for easier assembly etc
3. LCD should go to 5VDC not 3.3VDC (DONE)
4. Use fiber optics to see Huzzah LEDs
5. Plan mounting holes for peripheral board (TBD)
6. Draw design in mirror image (DONE)
7. Figure out how to port circuit to Fusion for better board design and milling
8. "uncross" the I2C wires for the LCD so we can use a straight through 4 pin connector with solid end connectors. Likely the LCD will be replaced with an OLED or two so wiring will need to be revisited anyhow.
9. Make use of touch sensors for diagnostic mode etc.
10. Move battery connection to main board
11. Use right angle headers for some cables such as the LCD
12. Put LED resistors and LEDs flush to the bard to eliminate strain on PCB traces and improve LED view-ability.
13. Maximize space around soldering leads for easier construction of board
14. Investigate bridging grounds between battery and USB jack so that console works on battery power as well as USB power.
15. Add power level monitoring for battery
16. Put a safety diode between the battery and the rest of the circuit.
17. Re-arrange position of motor controllers to avoid HUzzah32 console cable.

va3wam, 2018-11-17:
Updated this task to track all board design enhancement ideas that can be used for the next iteration of main and peripheral boards.

va3wam, 2019-05-04:
Doug, I think we can close this issue off now can we not?

va3wam, 2019-05-04:
Actually, I think that these are the items that you have left to deal with based on  the last email you sent to me...

-convert this list to tasks in git
-parts list
-verify latest layouts
-front panel designs
-cables that need to be made
-is pinouts doc up-to-date and complete
-document values for all resistors and caps
-components physical clearance
-are motor controllers calibratable in place
-are cables and headers keyed, marked, consistent?
-can we get/make a cable for switches/leds?

Closed 2019-06-17.

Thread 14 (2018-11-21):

Inconsistent variable behavior

va3wam, 2018-11-21:
The t0_per_sec variable sometimes has an invalid value of 0 and other times has a valid value of ~50K. Further investigation shows that if the I2C bus definitions come first in setup() then the timer moves to priority 0 on core0 and never runs. If the timer is defined first then the second I2C bus generates a HAL 261 error and is unusable.

va3wam, 2018-11-26:
I believe I have isolated the issue. It appears as if Timer0 conflicts with the second I2C bus used to communicate with the MPU6050. Note that simply defining the second bus causes the issue so it does not appear to be work load related. I tried abandoning the use of TwoWire() library in favour of the Wire() library but I see the exact same issue. Further investigation into the nature of the conflict and what option will best eliminate it is ongoing.

nerdoug, 2018-11-26:
I don't understand the conflict, but I notice that the examples I see on
the net use a variety of pins for the second I2C bus, but I can't find
anyone using the same ones we do. Maybe we should try some of these other
pin assignments?

---From our code:
#define SDA1 23
#define SCL1 22
#define SDA2 4
#define SCL2 5
TwoWire I2Cone = TwoWire(0);
TwoWire I2Ctwo = TwoWire(1);

--- from https://github.com/espressif/arduino-esp32/issues/977
1)

TwoWire I2Cone = TwoWire(0);
TwoWire I2Ctwo = TwoWire(1);
void setup() {
  I2Cone.begin(21,22,100000); // SDA pin 21, SCL pin 22, 100kHz frequency
  I2Ctwo.begin(16,17,400000); // SDA pin 16, SCL pin 17, 400kHz frequency

2)

#include <Wire.h>
#include <dummy.h>  //for esp32
#define SDA1 21
#define SCL1 22
#define SDA2 5
#define SCL2 4

TwoWire I2Cone = TwoWire(0);
TwoWire I2Ctwo = TwoWire(1);

---from https://github.com/espressif/arduino-esp32/issues/1438

The actual configuration will require one port to be a master and one port
to be a slave.

And thoughts or insights?
Sketch:

#include <Arduino.h>

#include <Wire.h>

#include <dummy.h> //for esp32

#define SDA1 21
#define SCL1 22
//#define SDA1 19
//#define SCL1 23

#define SDA2 19
#define SCL2 23

TwoWire1 I2Cone = TwoWire1(0);
TwoWire2 I2Ctwo = TwoWire2(1);

--- from https://randomnerdtutorials.com/esp32-esp8266-i2c-lcd-arduino-ide/

Wire your LCD to the ESP32 by following the next schematic diagram.

We’re using the ESP32 default I2C pins (GPIO 21 and GPIO 22).

(on a different ESP32 board: ESP32 DOIT DEVKIT V1 Board
<https://makeradvisor.com/tools/esp32-dev-board-wi-fi-bluetooth/> )

[image: image.png]

<delliott@nds.com>

I'm going to see if I can find some Expressif documentation that suggests
particular pins.

Cheers,
    Doug Elliott  VA3DAE
    cell & text: 519-630-8925
    email: canoe.eh@gmail.com
    web:  http://nerdpit.ca

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

va3wam, 2018-11-27:
Behavior: We have refined the behavior to this:
If the I2C bus definitions come first then the timer moves to priority 0 on core0 and never runs. If the timer is defined first then the second I2C bus generates a HAL 261 error.

Cause:
In summary the issue is that using a hardware timer plus two I2C buses caused resource challenges.
In detail, this issues appears to be tied to a known issue with the i2c HAL. A fix has been submitted (see https://github.com/espressif/arduino-esp32/pull/1877). This fix was submitted on September 21, 2018 and our PlatformIO ESP32 bundle does not include the fix. We know this because when you look at the affected file on Andrew's hard drive (/Users/andrewmitchell/.platformio/packages/framework-arduinoespressif32/cores/esp32/esp32-hal-i2c.c) we see this chunk of code:

    if(!i2c->intr_handle) { // create ISR for either peripheral
        // log_i("create ISR %d",i2c->num);
        uint32_t ret = 0;
        uint32_t flags = ESP_INTR_FLAG_EDGE |  //< Edge-triggered interrupt
          ESP_INTR_FLAG_IRAM |  //< ISR can be called if cache is disabled
          ESP_INTR_FLAG_LOWMED;   //< Low and medium prio interrupts. These can be handled in C.

which should be chnaged to
    if(!i2c->intr_handle) { // create ISR for either peripheral
        // log_i("create ISR %d",i2c->num);
        uint32_t ret = 0;
        uint32_t flags = ESP_INTR_FLAG_IRAM |  //< ISR can be called if cache is disabled
          ESP_INTR_FLAG_LOWMED |   //< Low and medium prio interrupts. These can be handled in C.
          ESP_INTR_FLAG_SHARED; //< Reduce resource requirements, Share interrupts

Fix: We need to use this updated ESP32 image so we need to figure out how to do that until PlatformIO updates to the latest image.

va3wam, 2018-11-28:
Changed /Users/andrewmitchell/.platformio/packages/framework-arduinoespressif32/cores/esp32/esp32-hal-i2c.c code from

    if(!i2c->intr_handle) { // create ISR for either peripheral
    // log_i("create ISR %d",i2c->num);
    uint32_t ret = 0;
    uint32_t flags = ESP_INTR_FLAG_EDGE |  //< Edge-triggered interrupt
      ESP_INTR_FLAG_IRAM |  //< ISR can be called if cache is disabled
      ESP_INTR_FLAG_LOWMED;   //< Low and medium prio interrupts. These can be handled in C.
to
    if(!i2c->intr_handle) { // create ISR for either peripheral
    // log_i("create ISR %d",i2c->num);
       uint32_t ret = 0;
       uint32_t flags = ESP_INTR_FLAG_IRAM | //< ISR can be called if cache is disabled
       ESP_INTR_FLAG_LOWMED | //< Low and medium prio interrupts. These can be handled in C.
       ESP_INTR_FLAG_SHARED; //< Reduce resource requirements, Share interrupts
as documented here: (see espressif/arduino-esp32#1877). We now must track these changes until the stable branch of ESP-IDF includes them.

Closed 2018-11-28.

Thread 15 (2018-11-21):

IMU not aligned properly

va3wam, 2018-11-21:
With the new version of TWIPi the axis which we need to use to balance the robot has changed. At present the balancing logic triggers when the robot is turned side to side rather than front to back. We just need to change which axis we are using to sense the robots balance.

va3wam, 2018-11-28:
Version 2.2.2 now has the gyro and accelerometer registers changed to accommodate the new orientation of the IMU in the robot chassis.

Closed 2018-11-28.

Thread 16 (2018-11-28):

Fix motor screws

va3wam, 2018-11-28:
Just put Locktite on the screws to stop them coming loose.

va3wam, 2019-01-03:
Used a bunch of lock-tite to cement things into place. Still not great but workable. e have new motors and proper M3 screws for the next chassis so this issue will be resolved.

Closed 2019-01-03.

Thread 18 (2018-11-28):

Create  second TWIPi

va3wam, 2018-11-28:
So we can both play with TWIPi!

va3wam, 2018-12-05:
Bought some MDF for this. Am also working on updated design that fixes a few things like better motor housing.

va3wam, 2019-06-18:
Have enough Acetron GP and complete CAM files for Chassis as well as the main board. Waiting on PCU-rev2 board tooling to come in. Once the first bot is fully underway I will kick off the second chassis.

va3wam, 2019-09-28:
We now have 2 chassis ready to go. There are some minor variances between the two but they are largely identical.

Closed 2019-09-28.

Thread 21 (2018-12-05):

One wheel is gimpy

va3wam, 2018-12-05:
During testing one wheel seems to spin more than the other

va3wam, 2019-01-03:
Issue was low battery. Put fully charged battery in and the issue went away.

Closed 2019-01-03.

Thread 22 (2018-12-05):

Motor mounting screw loose

va3wam, 2018-12-05:
We cannot properly seat the screws in the motor housing and as a result the motors are misaligned a bit and wiggle. This could affect our efforts to balance the robot.

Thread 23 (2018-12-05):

Calibration of IMU is off

va3wam, 2018-12-05:
Wheels turn during sideways movement. Swapping of axis that we did from SBS Mark2 may not have been done correctly.

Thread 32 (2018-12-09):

solder the mounting lugs on Peripheral board for switches / jacks

nerdoug, 2018-12-09:
The USB jack is now intermittent, and code can't be uploaded. The jack takes some stress when the cable is inserted and removed, and I suspect some of the leads have pulled loose. Two steps needed:
1) resolder the 4 leads from the jack to the Peripheral Board
2) solder the mounting lugs for the USB jack ) and the switches while you're at it) to provide physical stress relief for the devices accessible through the front of TWIPi

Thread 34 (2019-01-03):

Use inter-board connectors other than 25pin SUB-D

va3wam, 2019-01-03:
Pick new "daughter board" connection parts. Likely copy what Arduino boards use to connect daughter boards. Think of using different numbers of pins arrange asymmetrically so that there is only one way to mate the two boards.

nerdoug, 2019-04-30:
This is completed in the single board version (SB3) we're now using. It uses a smaller, keyed connector to connect to the switches, USB jack and LEDs that are externally accessible.

Closed 2019-04-30.

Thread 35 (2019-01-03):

Separate display board from MB and PB

va3wam, 2019-01-03:
Take the user interface parts of the current Peripheral Board and move them to a separate small board so we have more control over changing the interface without needing to redesign the other boards every time.

va3wam, 2019-05-04:
I think we can close this issue as Doug has now created SB3 which accommodates off-board lights and switches and the latest Chassis has a separate control panel to make changing the switches and lights separate from milling the rest of the chassis.

Closed 2019-05-04.

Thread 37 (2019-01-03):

Investigate industry standard trace width

va3wam, 2019-01-03:
Figure out what size traces we should use on our boards. This goes hand in hand with figuring out how to use Fusion to create boards rather than rely on FlatCAM.

nerdoug, 2019-03-13:
Used 2 online tools to evaluate trace with needed for the heavy-duty traces, the ones that carry motor current, both 12V and ground. The tools and parameters are shown in the 2nd and 3rd sheets of the cad-conversions.ods spreadsheet. Net result is that we need 50 mil wide traces for these paths.

For other traces, I used the following parameters in the ninja tool:
.5 Amp current
20 degree C temperature rise
1.6 mm board thickness
32 um track thickness
no plane present
0.2 thermal conductivity

and got a minimal Track width of 2.1 mils or 0.053 mm. We're now using 16 mil track width, so we have lots of safety margin.

Closed 2019-03-13.

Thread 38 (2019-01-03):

Find new battery connector option

va3wam, 2019-01-03:
Looking for a quick connect option for the new Mastercraft batteries we are going to be using. See part number 2823492000 Wiring Harness Assembly.

va3wam, 2019-01-03:
Wire Harness Assembly = Part Number 2823492000
Drive Bracket = Part Number 3124876000

Figuring out where to buy this stuff is another matter entirely

Closed 2019-06-17.

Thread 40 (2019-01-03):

Settle on new battery to use

va3wam, 2019-01-03:
Need to give Doug his batteries back!

va3wam, 2019-01-03:
We are using the Mastercraft 20V max Lithium-ion battery. It comes in both 2.0aH and 4.0aH flavors.

Closed 2019-01-03.

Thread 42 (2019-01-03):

Convert from main.ino to main.cpp file

va3wam, 2019-01-03:
We are now using VSC as our editor and as such are no longer required to use .INO as a file extension for our Arduino code. The Platform.IO plugin we use prefers that we use .CPP so we should move to that.

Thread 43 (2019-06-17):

Document how to fix pads in Eagle

va3wam, 2019-06-17:
Doug has figured out why sometimes pads on a PCB are missing. Lets document the process so I can put it on the Wiki along with all our other helpful tips.

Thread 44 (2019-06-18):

Create the PCU_REV2

va3wam, 2019-06-18:
1. Wait for the new collets and collet holders to arrive
2. Set up the following drills in Pathpilot and Fusion (also in your spreadsheet in Github)
- D8 is a 1mm drill used for Power cable headers, USB jack mounting lugs and pin headers/vias
- D10 is a 1.2mm drill used for Push-button switches
- D11 is a 5/64” drill used for the mounting holes
- D12 is a 3/32” drill used for Ribbon cable connector, USB cable pins
- D13 is a 19/32” drill used for Diodes
3. Update the tools assigned to the D8 through D13 tool in the 01_TopFaceUp
4. Mill the PCB and celebrate our first 2 sided PCB

va3wam, 2019-06-18:
Will do this when I return in 10 days or so

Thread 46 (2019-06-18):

Create SB5 PCB for first robot

va3wam, 2019-06-18:

va3wam, 2019-12-27:
Update from Dooug:
-console connection works whether power is from battery or USB
-main voltage regulator is set up, with a 3A current limit
-have a voltmeter /  current meter built in to my test jig, showing
 voltage and current coming out of main regulator
-the Red pushbutton doesn't light up, likely as a result of a bunch of
 soldering rework I did cooking the LED. I don't think it's critical.
-s/w readable pushbutton and s/w controlled LED tested and working.
-have calibrated motor controllers so the maximum current is 3A.
 They were originally set to Vref = 1.6V, but after some math, I set
 them to .53V, which might be wrong, but is definitely conservative.
-In my spare moments, I'm trying to get the IMU working by transferring
 code snippets from Twipi's source. Still working on that.

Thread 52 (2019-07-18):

Circuit board - SBx - Add second I2C header for 2 OLED's

va3wam, 2019-07-18:
We are replacing the single monochrome LCD with two monochrome OLED's which will act as eyes as well as monitors. We can do this by either adding a second set of headers to the I2C bus on the board or with a slitter cable.

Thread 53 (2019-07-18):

PCB - SBx - externalize battery power regulator

va3wam, 2019-07-18:
We have new 5AMP power regulators for battery connections which are big enough that we should consider mounting them away from the SBx board. This has implications to the circuit board that need to be reviewed.

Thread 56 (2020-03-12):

Finish SB7 boards for both robots

va3wam, 2020-03-12:
- solder push buttons onto 2nd PCB
- solder USB PCB connectors to both boards on parts arrival
- attach battery wires to battery terminals on chassis
- put female connectors on stepper motors, on both robots
- connect 2 cable harnesses to voltage regulator boards
- connect battery power cable to voltage regulators
- mount voltage regulator boards on each robot
- solder pins onto second ESP32 (survey inventory)

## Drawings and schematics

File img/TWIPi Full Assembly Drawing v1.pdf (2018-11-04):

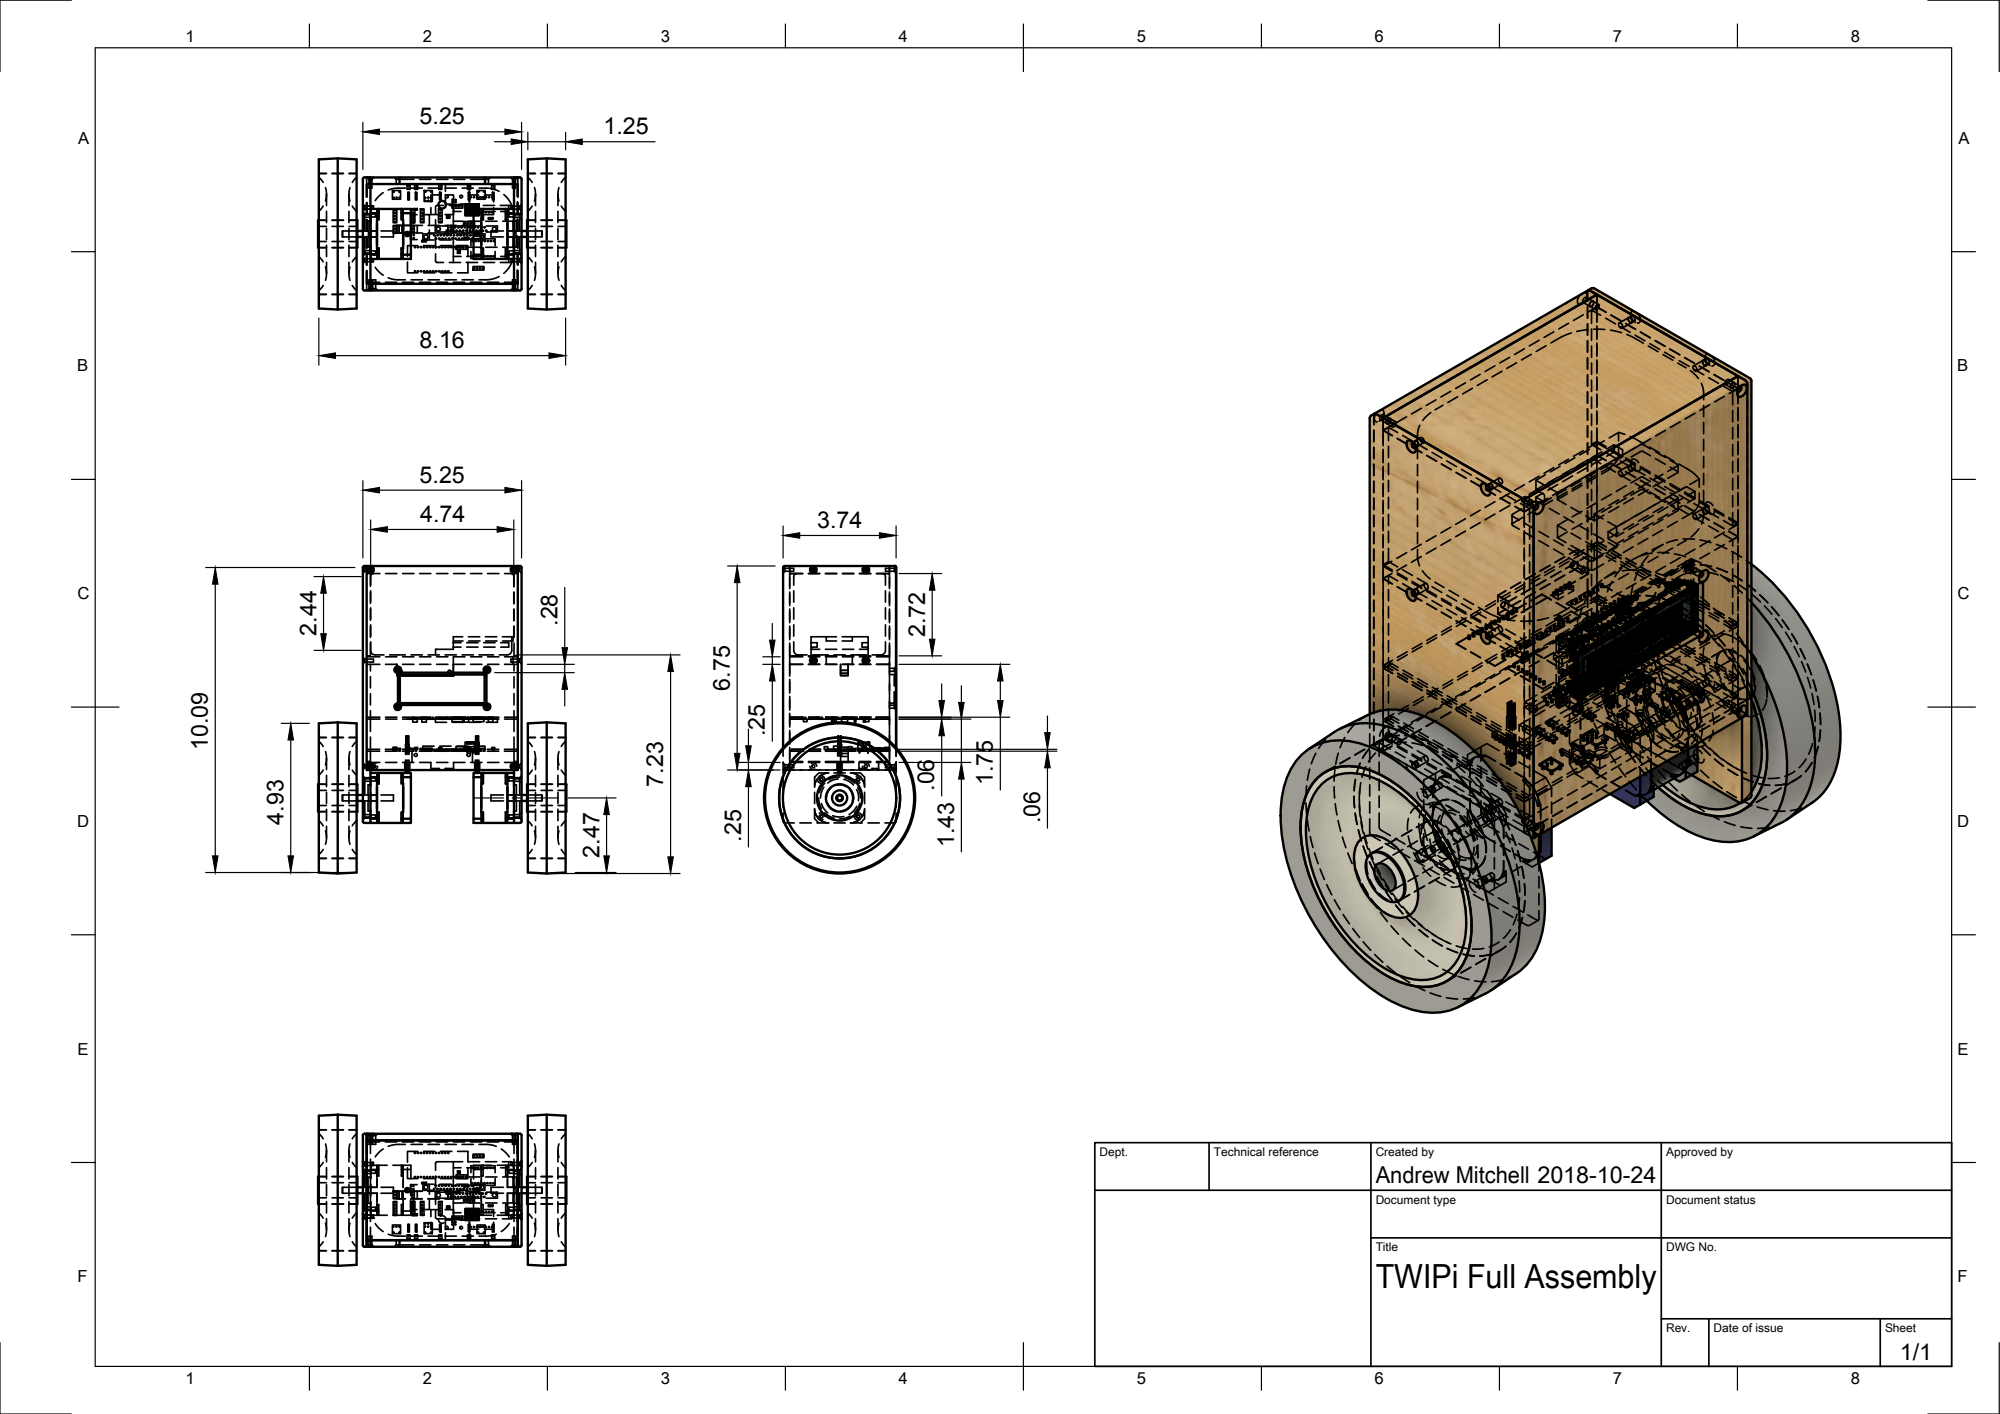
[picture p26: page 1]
Dept.; Technical reference; Created by; Approved by; Document type; Document status; Title; DWG No.; Rev.; Date of issue; Sheet; Andrew Mitchell 10.09

TWIPi Full Assembly

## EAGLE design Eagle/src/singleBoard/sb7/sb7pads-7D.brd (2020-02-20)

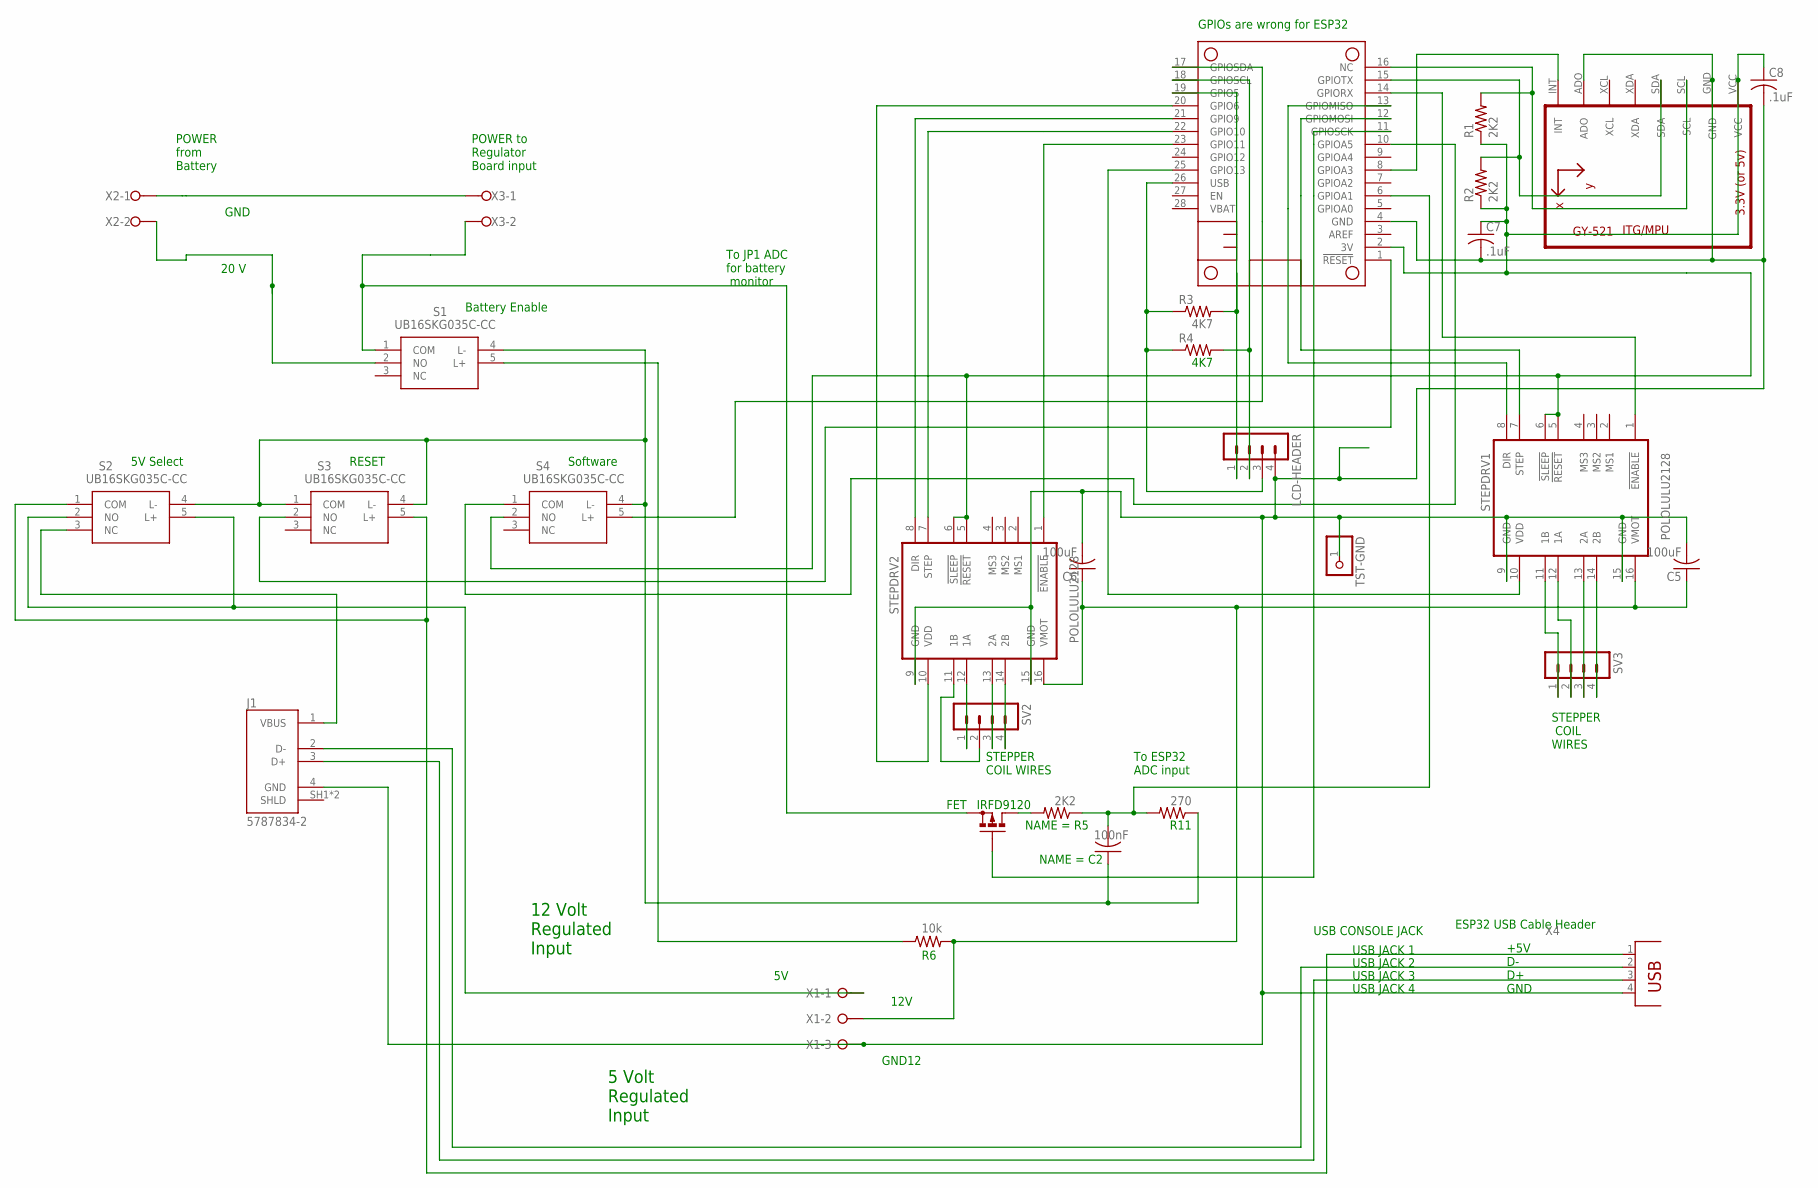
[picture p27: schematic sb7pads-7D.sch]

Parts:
C2: 100nF; C050-025X075
C5, C6: 100uF; C050-024X044
C7, C8: .1uF; C050-024X044
FET: IRFD9120; C370-01
J1: 5787834-2; TE_5787834-2
LCD-HEADER: MA04-1
MS2: FEATHERWING_NOHOLES
R1, R2: 2K2; 0309/12
R3, R4: 4K7; 0309/12
R5: 2K2; 0207/10
R6: 10k; 0207/10
R11: 270; 0207/10
S1, S2, S3, S4: UB16SKG035C-CC; UB16SKG035CCC
STEPDRV1, STEPDRV2: POLOLULU2128
SV2, SV3: MA04-1
TST-GND: 1X01
U1: GY-521MPU6050; GY-521
X1: W237-3E
X2, X3: W237-02P; W237-132
X4: PN87520

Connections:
3V: C7.1, C8.1, MS2.2 (3V), R1.1, R2.1, S4.2 (NO), STEPDRV1.5 (!RESET), STEPDRV1.6 (!SLEEP), STEPDRV2.5 (!RESET), STEPDRV2.6 (!SLEEP), U1.VCC
unnamed: MS2.25 (GPIO13), STEPDRV1.10 (VDD)
unnamed: FET.G, MS2.11 (GPIOSCK)
unnamed: S1.2 (NO), X2.2
unnamed: MS2.1 (!RESET), S3.2 (NO)
unnamed: MS2.21 (GPIO9), STEPDRV2.8 (DIR)
unnamed: FET.S, S1.1 (COM), X3.2
unnamed: MS2.14 (GPIORX), STEPDRV1.1 (!ENABLE)
unnamed: STEPDRV2.14 (2B), SV2.4
unnamed: STEPDRV2.12 (1A), SV2.1
unnamed: LCD-HEADER.1, MS2.19 (GPIO5), R3.2
unnamed: STEPDRV2.13 (2A), SV2.3
unnamed: STEPDRV2.11 (1B), SV2.2
unnamed: MS2.8 (GPIOA3), U1.INT
unnamed: MS2.12 (GPIOMOSI), STEPDRV1.7 (STEP)
unnamed: STEPDRV1.14 (2B), SV3.4
unnamed: MS2.16 (NC), R1.2, U1.SCL
unnamed: STEPDRV1.13 (2A), SV3.3
unnamed: STEPDRV1.12 (1A), SV3.2
unnamed: STEPDRV1.11 (1B), SV3.1
unnamed: X2.1, X3.1
unnamed: J1.2 (D-), X4.2
unnamed: J1.3 (D+), X4.3
unnamed: MS2.13 (GPIOMISO), STEPDRV1.8 (DIR)
unnamed: MS2.15 (GPIOTX), R2.2, U1.SDA
unnamed: C5.2, C6.2, C7.2, C8.2, J1.4 (GND), LCD-HEADER.4, MS2.4 (GND), STEPDRV1.9 (GND), STEPDRV1.15 (GND), STEPDRV2.9 (GND), STEPDRV2.15 (GND), TST-GND.1, U1.ADO, U1.GND, X1.3, X4.4
unnamed: S2.2 (NO), S2.5 (L+), X1.1
unnamed: MS2.17 (GPIOSDA), S4.5 (L+)
unnamed: C2.2, MS2.6 (GPIOA1), R5.1, R11.2
unnamed: R6.1, S1.5 (L+)
unnamed: S2.1 (COM), S3.5 (L+), X4.1
unnamed: MS2.22 (GPIO10), STEPDRV2.7 (STEP)
unnamed: LCD-HEADER.2, MS2.18 (GPIOSCL), R4.2
unnamed: MS2.20 (GPIO6), STEPDRV2.10 (VDD)
unnamed: MS2.23 (GPIO11), STEPDRV2.1 (!ENABLE)
unnamed: MS2.10 (GPIOA5), S4.1 (COM)
unnamed: C5.1, C6.1, R6.2, STEPDRV1.16 (VMOT), STEPDRV2.16 (VMOT), X1.2
unnamed: J1.1 (VBUS), S2.3 (NC)
unnamed: FET.D, FET.D1 (D), R5.2
unnamed: C2.1, R11.1, S1.4 (L-), S2.4 (L-), S3.1 (COM), S3.4 (L-), S4.4 (L-)
USB: LCD-HEADER.3, MS2.26 (USB), R3.1, R4.1

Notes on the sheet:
GPIOs are wrong for ESP32
STEPPER COIL WIRES
12V
GND12
ESP32 USB Cable Header
STEPPER COIL WIRES
To ESP32 ADC input
+5V D- D+ GND
To JP1 ADC for battery monitor
USB CONSOLE JACK
USB JACK 1
USB JACK 2
USB JACK 3
USB JACK 4
POWER from Battery
POWER to Regulator Board input
20 V
GND
Battery Enable
5V Select
RESET
Software
12 Volt Regulated Input
5 Volt Regulated Input

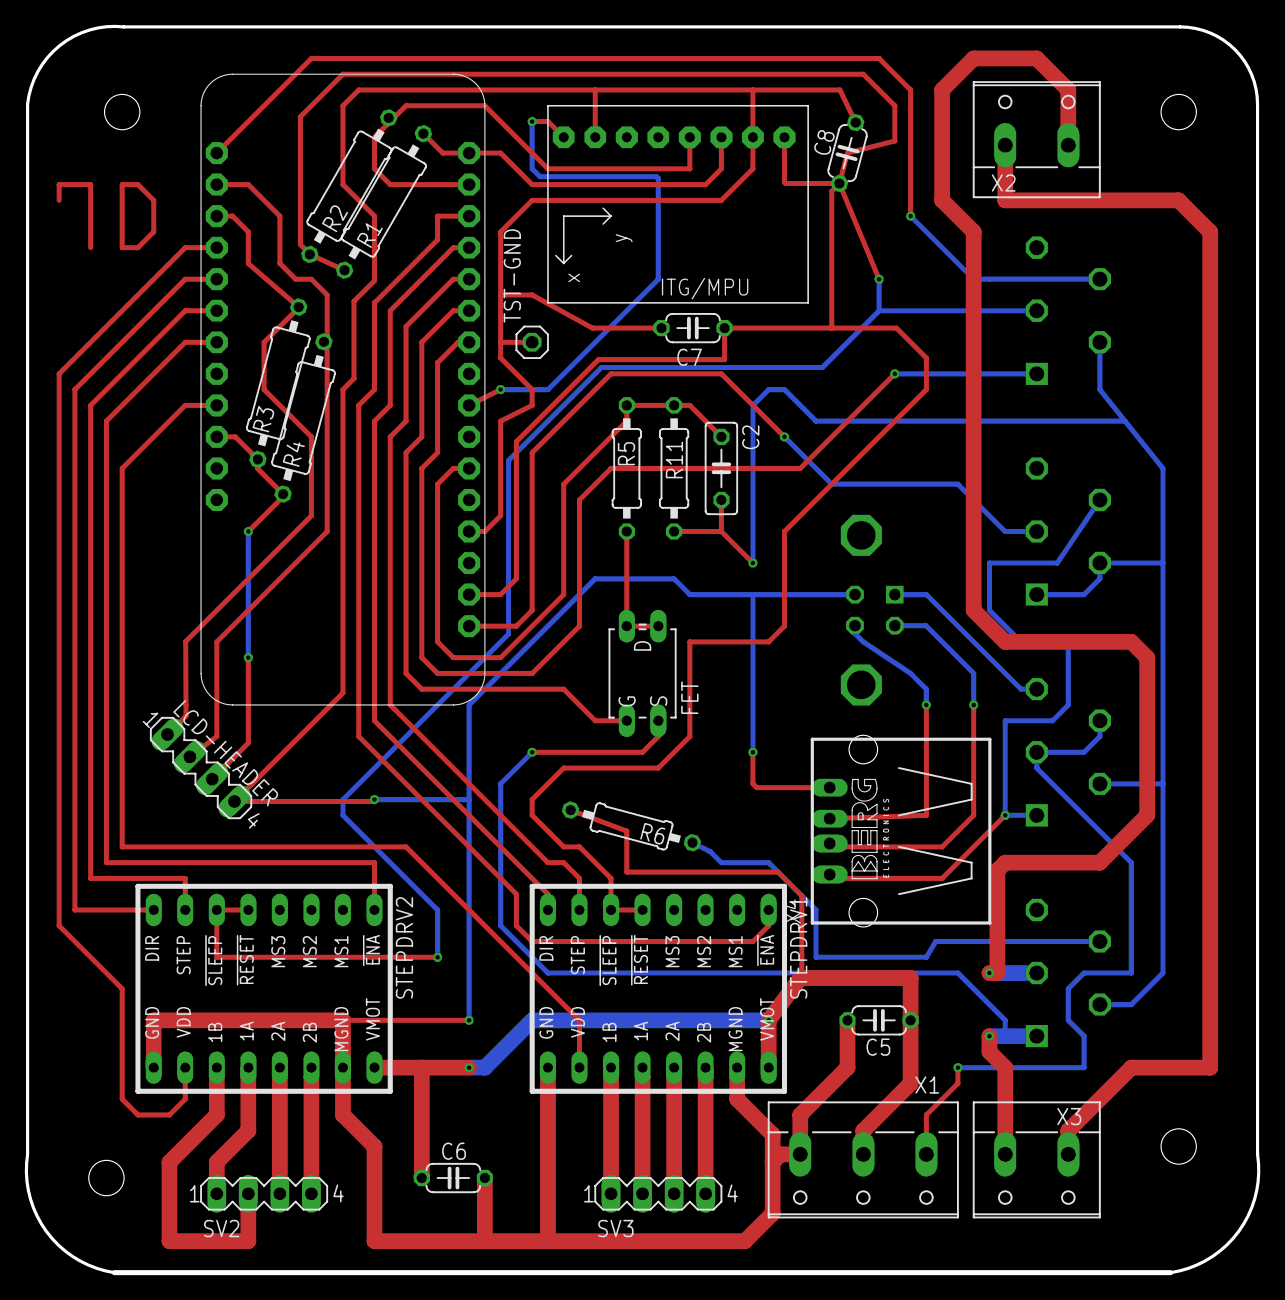
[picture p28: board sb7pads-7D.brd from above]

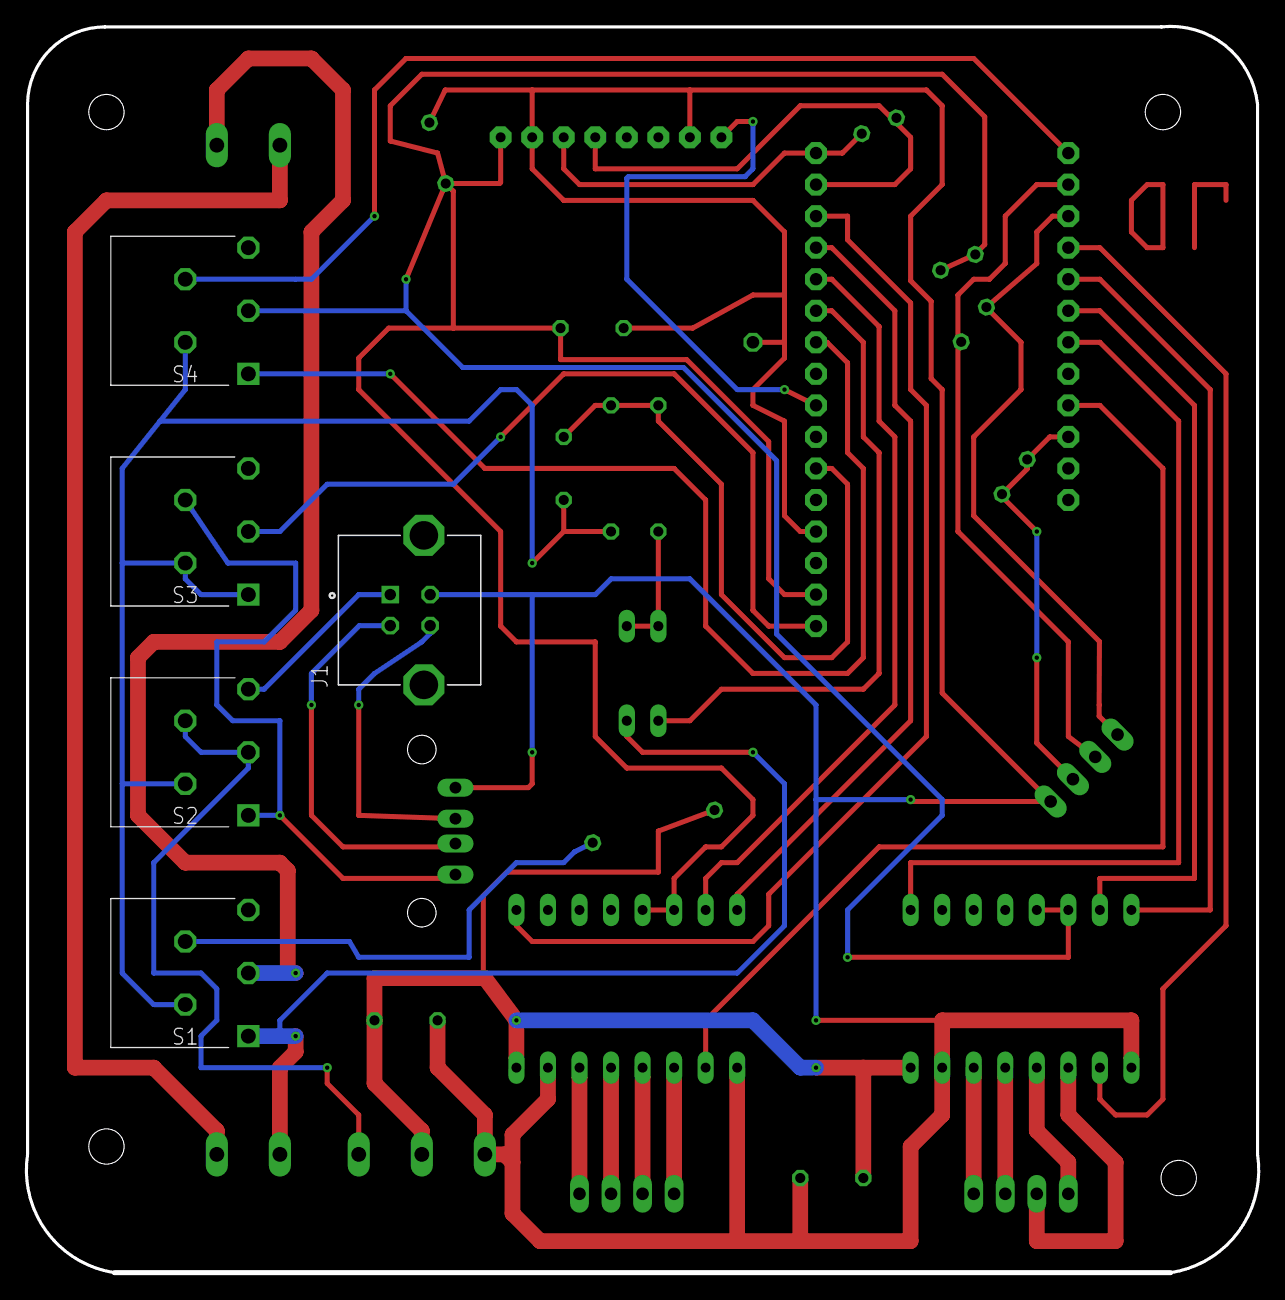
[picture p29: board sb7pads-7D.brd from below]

Board: 2 copper layers, 99.3 x 100.4 mm, 30 parts (5 on the bottom side), 41 nets.

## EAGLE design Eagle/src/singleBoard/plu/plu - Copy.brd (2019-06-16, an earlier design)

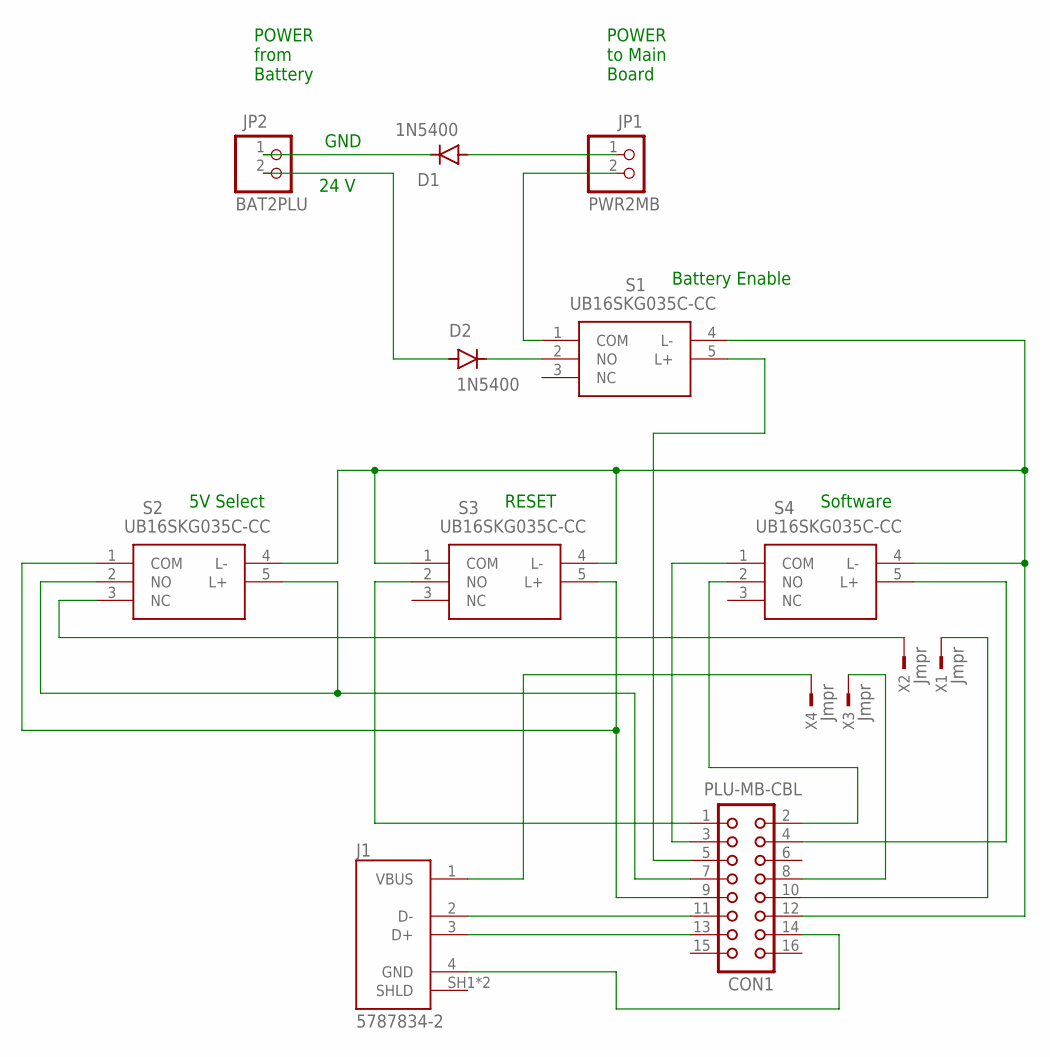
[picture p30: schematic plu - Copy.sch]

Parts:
CON1: PLU-MB-CBL; CON16
D1, D2: 1N5400; DO201-15
J1: 5787834-2; TE_5787834-2
JP1: PWR2MB; 1X02
JP2: BAT2PLU; 1X02
S1, S2, S3, S4: UB16SKG035C-CC; UB16SKG035CCC
X1, X2, X3, X4: Jmpr; TSW-101-XX-G-S

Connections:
unnamed: D1.A, JP1.1
unnamed: CON1.1, S3.2 (NO)
unnamed: D1.C, JP2.1
unnamed: D2.C, S1.2 (NO)
unnamed: D2.A, JP2.2
unnamed: JP1.2, S1.1 (COM)
unnamed: CON1.11, J1.2 (D-)
unnamed: J1.1 (VBUS), X4.1
unnamed: CON1.2, S4.2 (NO)
unnamed: CON1.3, S4.1 (COM)
unnamed: CON1.13, J1.3 (D+)
unnamed: CON1.4, S4.5 (L+)
unnamed: CON1.5, S1.5 (L+)
unnamed: CON1.14, J1.4 (GND)
unnamed: CON1.7, S2.2 (NO), S2.5 (L+)
unnamed: CON1.10, X1.1
unnamed: CON1.9, S2.1 (COM), S3.5 (L+)
unnamed: CON1.12, S1.4 (L-), S2.4 (L-), S3.1 (COM), S3.4 (L-), S4.4 (L-)
unnamed: S2.3 (NC), X2.1
unnamed: CON1.8, X3.1

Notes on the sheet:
POWER from Battery
POWER to Main Board
24 V
GND
Battery Enable
5V Select
RESET
Software

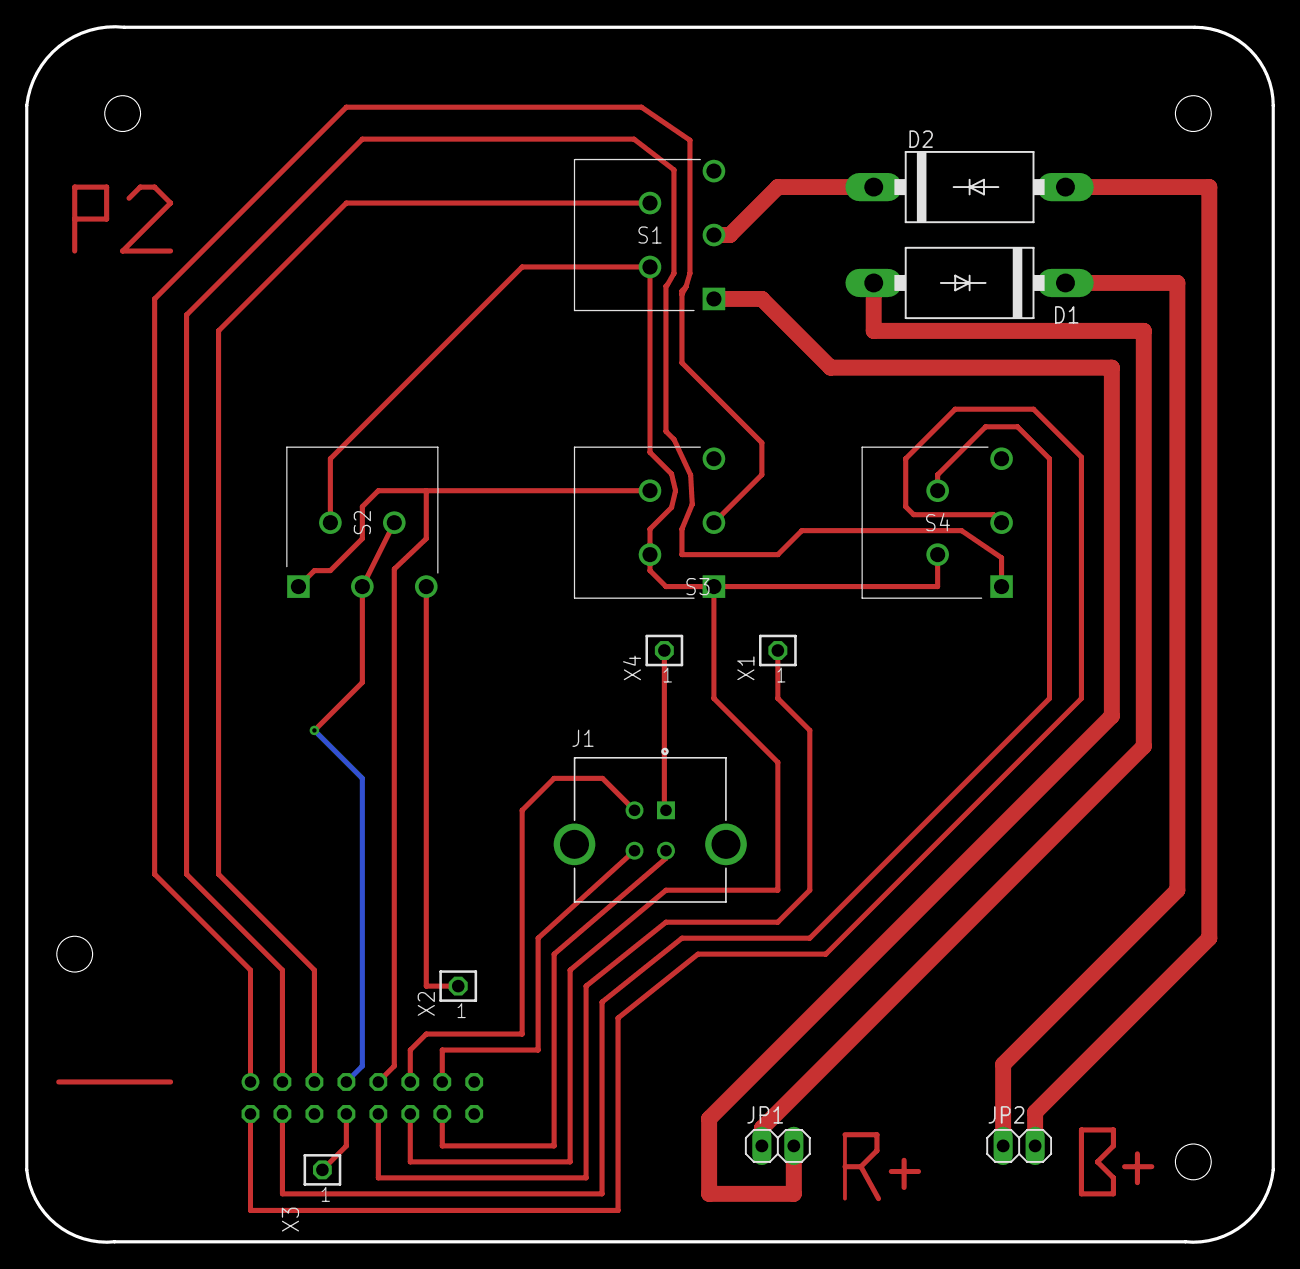
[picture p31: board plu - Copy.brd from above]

Board: 2 copper layers, 99.1 x 96.6 mm, 14 parts (1 on the bottom side), 20 nets.

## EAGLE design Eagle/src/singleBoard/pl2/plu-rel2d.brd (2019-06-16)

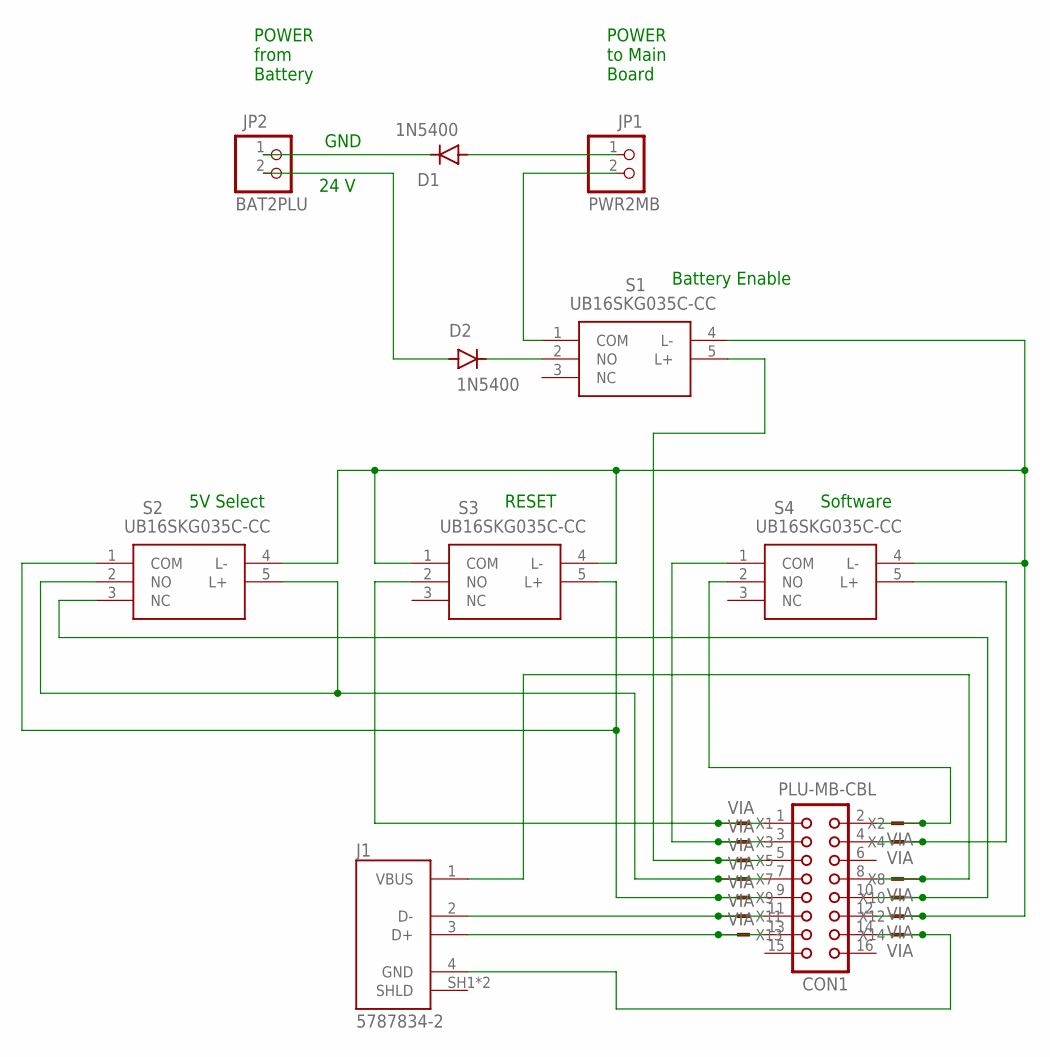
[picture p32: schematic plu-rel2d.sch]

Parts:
CON1: PLU-MB-CBL; CON16
D1, D2: 1N5400; DO201-15
J1: 5787834-2; TE_5787834-2
JP1: PWR2MB; 1X02
JP2: BAT2PLU; 1X02
S1, S2, S3, S4: UB16SKG035C-CC; UB16SKG035CCC
X1, X2, X3, X4, X5, X7, X8, X9, X10, X11, X12, X13, X14: VIA; TSW-101-XX-G-S

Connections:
unnamed: D1.A, JP1.1
unnamed: CON1.1, S3.2 (NO), X1.1
unnamed: D1.C, JP2.1
unnamed: D2.C, S1.2 (NO)
unnamed: D2.A, JP2.2
unnamed: JP1.2, S1.1 (COM)
unnamed: CON1.3, S4.1 (COM), X3.1
unnamed: CON1.2, S4.2 (NO), X2.1
unnamed: CON1.4, S4.5 (L+), X4.1
unnamed: CON1.8, J1.1 (VBUS), X8.1
unnamed: CON1.5, S1.5 (L+), X5.1
unnamed: CON1.7, S2.2 (NO), S2.5 (L+), X7.1
unnamed: CON1.9, S2.1 (COM), S3.5 (L+), X9.1
unnamed: CON1.10, S2.3 (NC), X10.1
unnamed: CON1.11, J1.2 (D-), X11.1
unnamed: CON1.13, J1.3 (D+), X13.1
unnamed: CON1.12, S1.4 (L-), S2.4 (L-), S3.1 (COM), S3.4 (L-), S4.4 (L-), X12.1
unnamed: CON1.14, J1.4 (GND), X14.1

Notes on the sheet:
POWER from Battery
POWER to Main Board
24 V
GND
Battery Enable
5V Select
RESET
Software

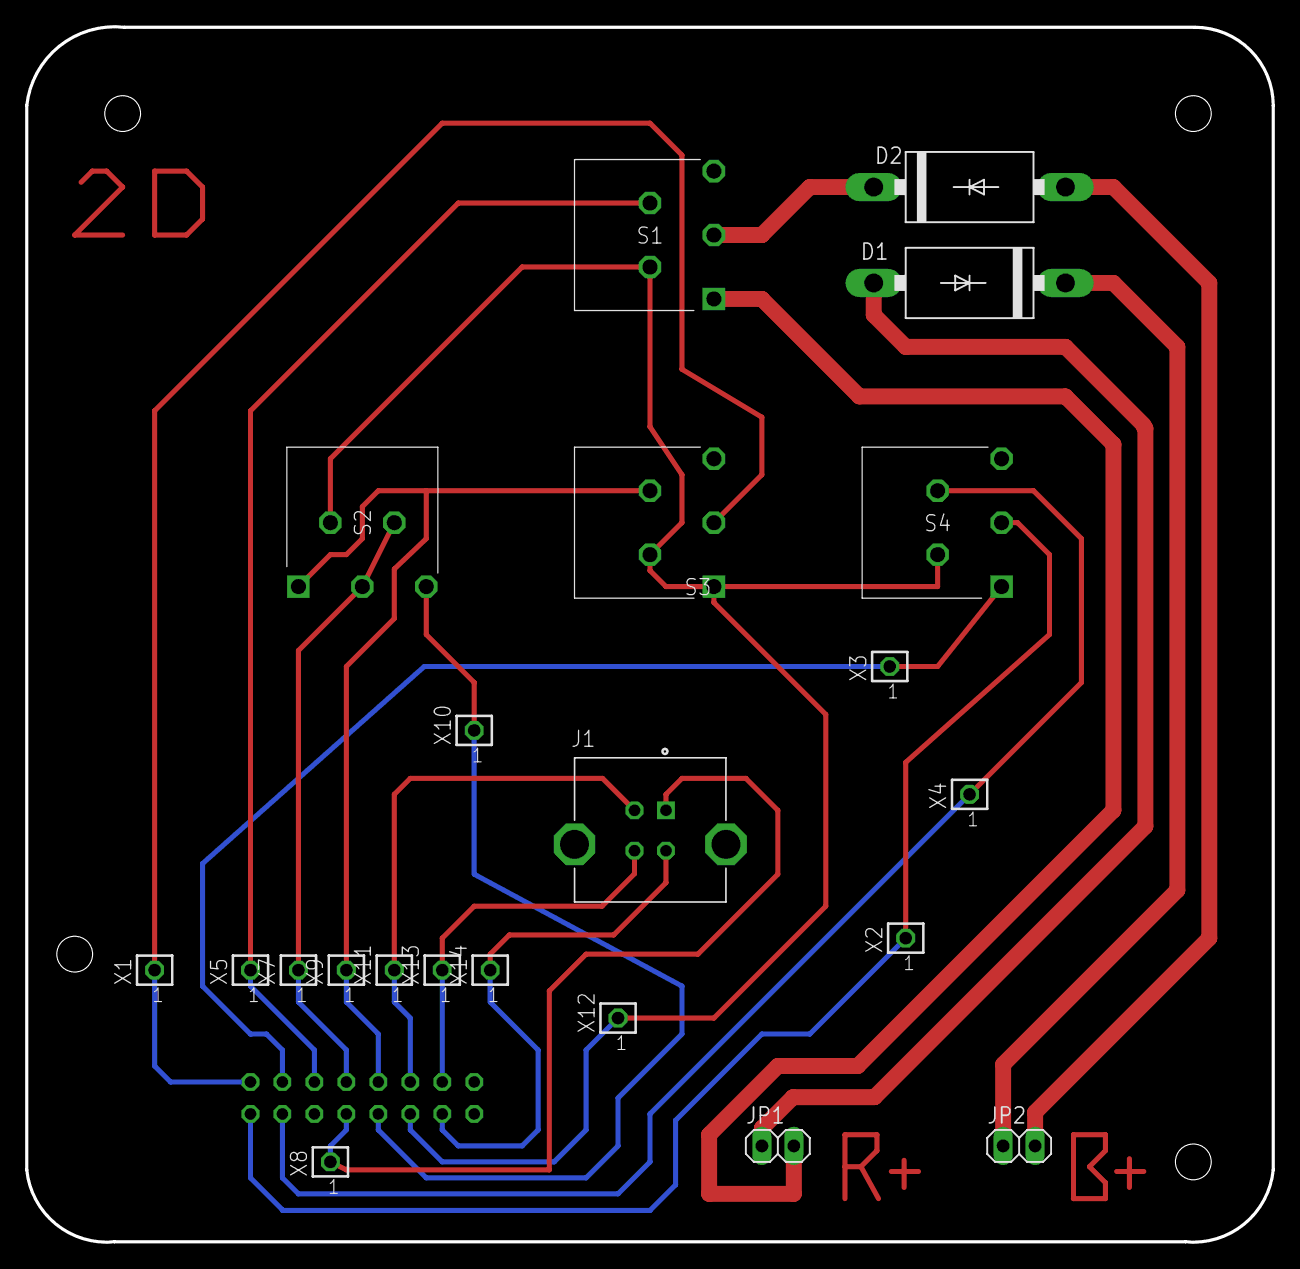
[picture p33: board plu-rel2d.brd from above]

Board: 2 copper layers, 99.1 x 96.6 mm, 23 parts (1 on the bottom side), 18 nets.

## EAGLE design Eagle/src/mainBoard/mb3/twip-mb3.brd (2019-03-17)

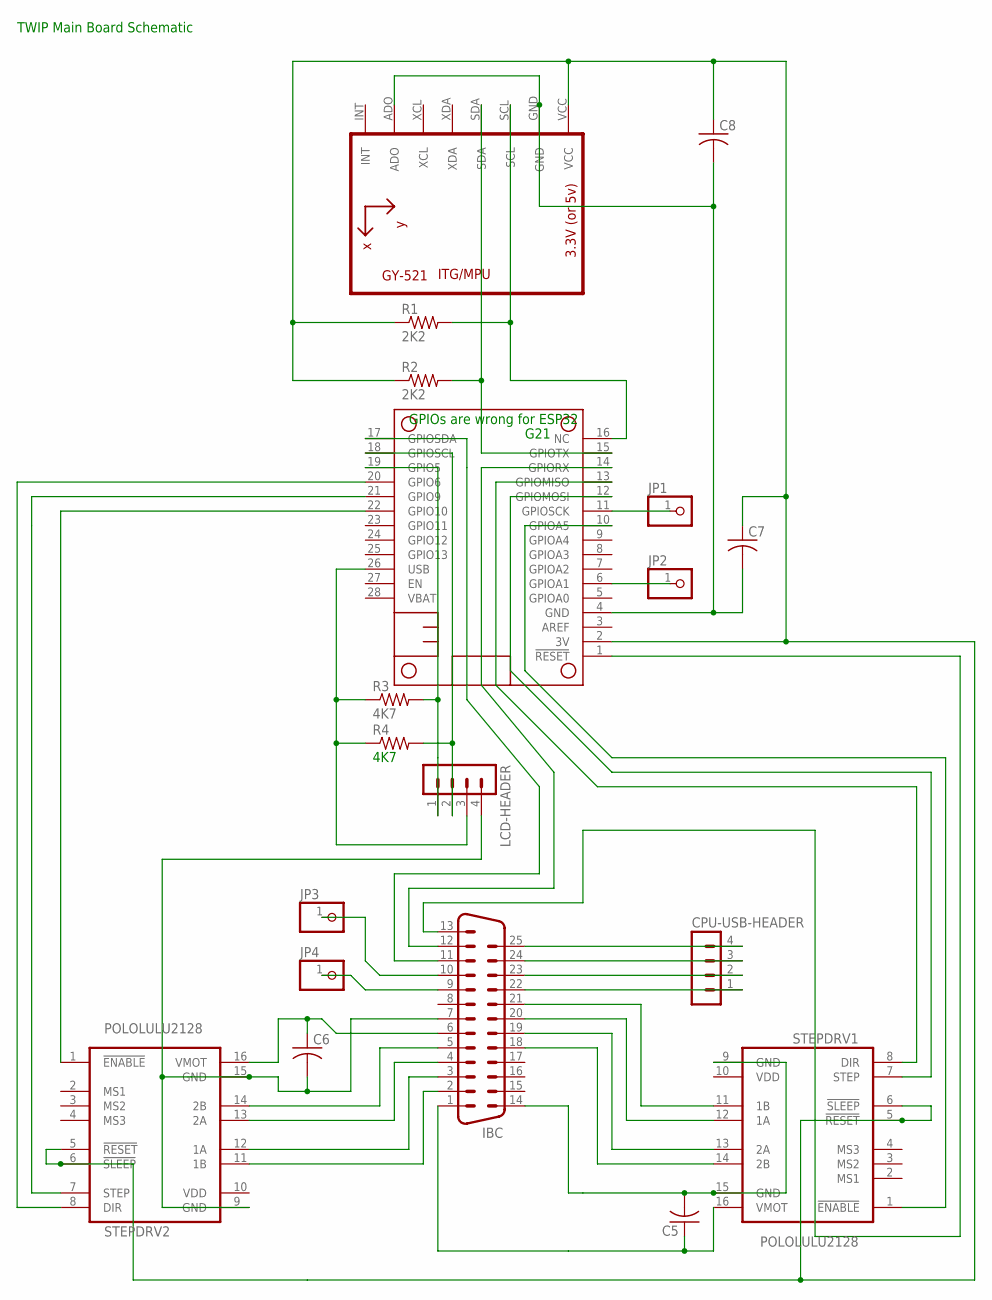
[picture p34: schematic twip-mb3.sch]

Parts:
C5, C6, C7, C8: C-US050-024X044; C050-024X044
CPU-USB-HEADER: MA04-1
IBC: M25VP
JP1, JP2, JP3, JP4: PINHD-1X1; 1X01
LCD-HEADER: MA04-1
MS2: FEATHERWING_NOHOLES
R1, R2: 2K2; 0309/12
R3, R4: 4K7; 0309/12
STEPDRV1, STEPDRV2: POLOLULU2128
U1: GY-521MPU6050; GY-521

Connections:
unnamed: C7.2, C8.2, MS2.4 (GND), U1.ADO, U1.GND
unnamed: IBC.18, STEPDRV1.14 (2B)
unnamed: IBC.19, STEPDRV1.13 (2A)
unnamed: MS2.12 (GPIOMOSI), STEPDRV1.7 (STEP)
unnamed: IBC.20, STEPDRV1.12 (1A)
unnamed: IBC.21, STEPDRV1.11 (1B)
unnamed: IBC.2, STEPDRV2.11 (1B)
unnamed: IBC.3, STEPDRV2.12 (1A)
unnamed: IBC.4, STEPDRV2.13 (2A)
unnamed: LCD-HEADER.1, MS2.19 (GPIO5), R3.2
unnamed: IBC.5, STEPDRV2.14 (2B)
unnamed: CPU-USB-HEADER.4, IBC.25
unnamed: CPU-USB-HEADER.3, IBC.24
unnamed: MS2.13 (GPIOMISO), STEPDRV1.8 (DIR)
unnamed: IBC.13, MS2.1 (!RESET)
unnamed: MS2.16 (NC), R1.2, U1.SCL
unnamed: CPU-USB-HEADER.2, IBC.23
unnamed: IBC.12, MS2.14 (GPIORX)
unnamed: C5.2, IBC.14, STEPDRV1.9 (GND), STEPDRV1.15 (GND)
unnamed: C6.1, IBC.6, STEPDRV2.16 (VMOT)
unnamed: C5.1, IBC.1, STEPDRV1.16 (VMOT)
unnamed: MS2.15 (GPIOTX), R2.2, U1.SDA
unnamed: MS2.20 (GPIO6), STEPDRV2.8 (DIR)
unnamed: IBC.11, MS2.17 (GPIOSDA)
unnamed: MS2.21 (GPIO9), STEPDRV2.7 (STEP)
unnamed: CPU-USB-HEADER.1, IBC.22
unnamed: MS2.10 (GPIOA5), STEPDRV1.1 (!ENABLE)
unnamed: JP1.1, MS2.11 (GPIOSCK)
unnamed: C6.2, IBC.7, LCD-HEADER.4, STEPDRV2.9 (GND), STEPDRV2.15 (GND)
unnamed: MS2.22 (GPIO10), STEPDRV2.1 (!ENABLE)
unnamed: LCD-HEADER.2, MS2.18 (GPIOSCL), R4.2
unnamed: JP2.1, MS2.6 (GPIOA1)
unnamed: IBC.10, JP3.1
unnamed: IBC.9, JP4.1
USB: LCD-HEADER.3, MS2.26 (USB), R3.1, R4.1

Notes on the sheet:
GPIOs are wrong for ESP32
G21
TWIP Main Board Schematic

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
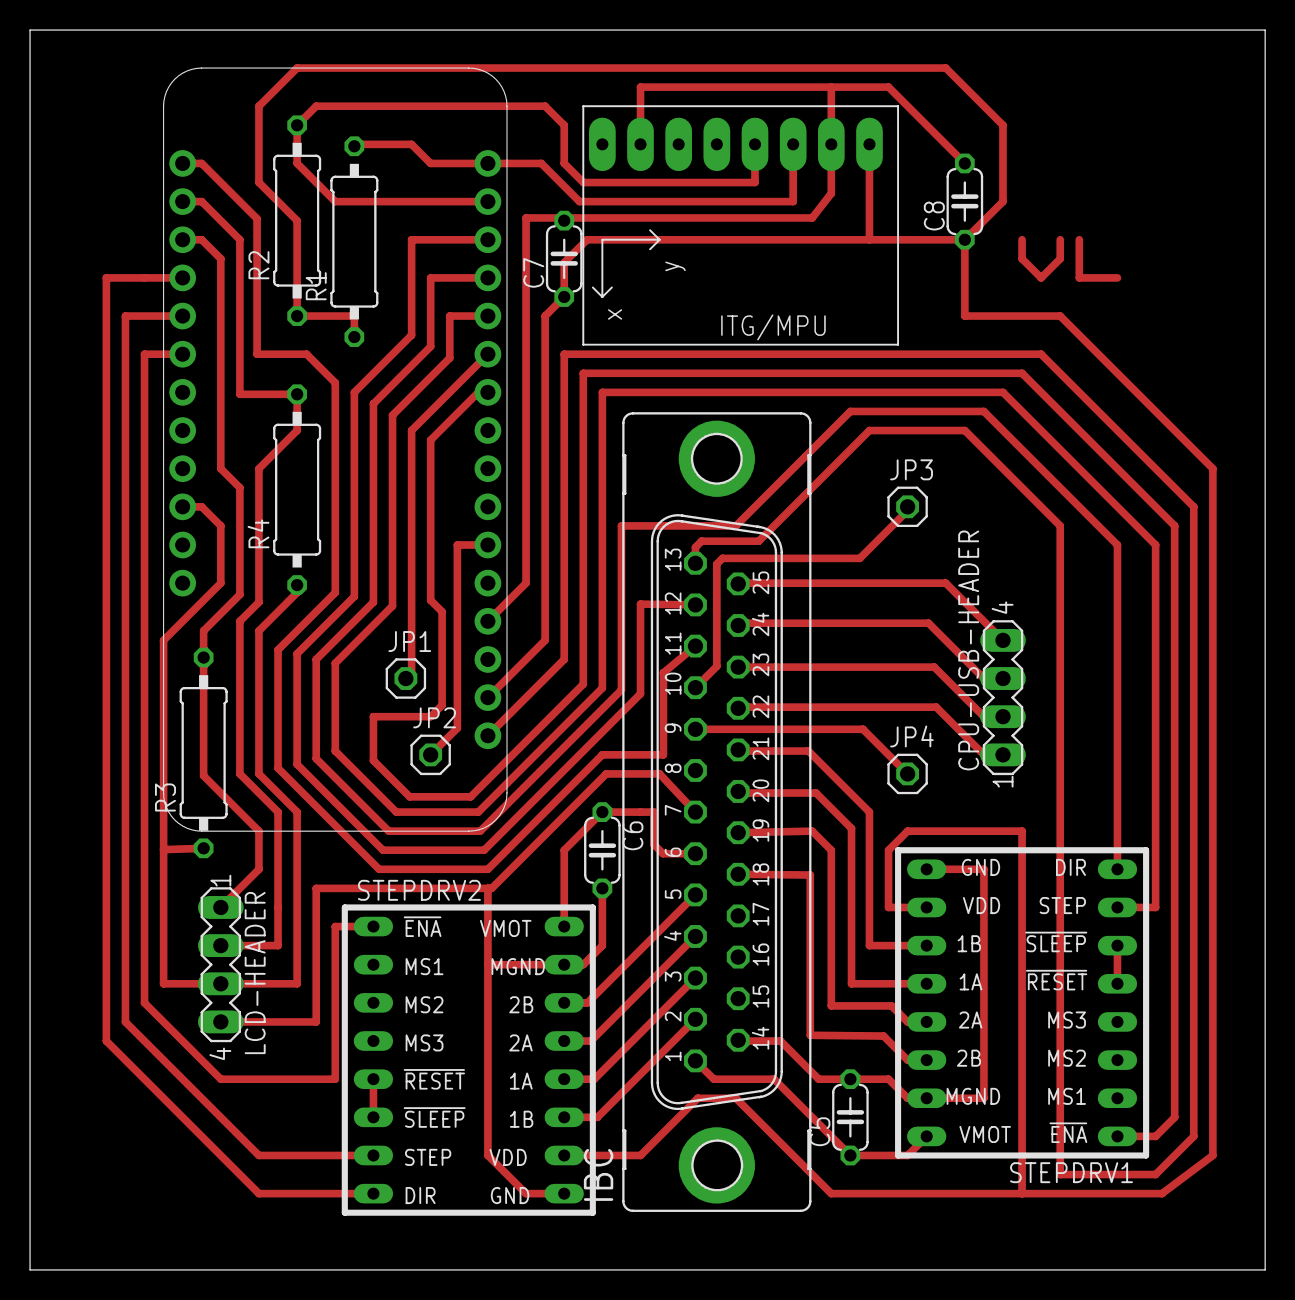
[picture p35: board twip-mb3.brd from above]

Board: 2 copper layers, 82.2 x 82.5 mm, 19 parts (0 on the bottom side), 38 nets.

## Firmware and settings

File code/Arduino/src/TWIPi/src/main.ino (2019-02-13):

/* Table of Contents ... egrep '^void|static void|volatile void' main.ino

void flashLCD();  // from http://forum.arduino.cc/index.php?topic=42835.0
static void writeLED(bool); // Define function that sets the onbard LED, accepts 0 or 1
void IRAM_ATTR onTimer0()
void display_Running_Sketch()
void writeLED(bool LEDon)
void startI2Cone()
void startI2Ctwo()
void initializeLCD()
void sendLCD(String LCDmsg, byte LCDline)
void scrollLCD(String LCDmsg, byte LCDline)
void flashLCD()
void hexdump(const void *mem, uint32_t len, uint8_t cols = 16)
void startWiFi()
void startDNS()
volatile void handleRoot()
volatile void handleNotFound()
void startWebServer()
void startWebsocket()
void webSocketEvent(uint8_t num, WStype_t type, uint8_t * payload, size_t length)
void process_Client_JSON_msg(uint8_t num, WStype_t type, uint8_t * payload, size_t length)
void sendClientPing(uint8_t num)
void sendClientLEDState(uint8_t num)
void sendClientLCDState(uint8_t num)
void reportTel(String msg)
void sendClientBalanceGraph(uint8_t num,float a1, float a2, float a3, float a4)
void sendClientVariableValue(uint8_t num, String variable)
void initializeIMU()
void set_gyro_registers()
void read_mpu_6050_data()
void startTimer0()
void initializeMotorControllers()
void setup()
void monitorWebsocket(void * parameter)
void monitorWeb(void * parameter)
void balanceRobot()
void loop()
*/

#include <Arduino.h>              // Required for platformIO Intellisense? Standard Arduino functions?
#include <WiFi.h>                 // Required to connect to WiFi network
#include <WiFiMulti.h>            // Allows us to try connecting to multiple Access Points
#include <ESP32WebServer.h>       // https://github.com/Pedroalbuquerque/ESP32WebServer
#include <ESPmDNS.h>              // Required for domain name service
#include <WebSocketsServer.h>     // https://github.com/Links2004/arduinoWebSockets
#include <Wire.h>                 // Needed for I2C communication
#include <LiquidCrystal_I2C.h>    // https://github.com/marcoschwartz/LiquidCrystal_I2C
#include <ArduinoJson.h>          // https://github.com/bblanchon/ArduinoJson

/***********************************************************************************************************
  Synopsis:
  This is the main sketch for the TWIPi robot. 

  NOTE!!! /Users/andrewmitchell/.platformio/packages/framework-arduinoespressif32/cores/esp32/esp32-hal-i2c.c
  has custom lines in it that differ from the ESP-IDF stable release. Make sure that these lines are 
  maintained when updating to the latest PlatformIO ESP-IDF files. Failure to do so will result in unrelaible
  I2C and hardware timer behavior. See the closing comments for issue https://github.com/va3wam/TWIPi/issues/14
  for full details.

  Environment:
  - Platform: Espressif 32 (https://www.espressif.com/en/products/hardware/esp32/overview)
  - Framework: Arduino 
  - Embedded board: Adafruit HUZZAH32 Feather (https://learn.adafruit.com/adafruit-huzzah32-esp32-feather/pinouts)
  - SOC: WROOM32 module (https://dl.espressif.com/doc/esp-idf/latest/hw-reference/modules-and-boards.html)
  - IDE: Visual Studio Code v1.27.2 (https://code.visualstudio.com/)
  - VSC plugin: platformIO v3.6.1a4 (https://platformio.org/platformio-ide)
  - RTOS: FreeRTOS (https://www.freertos.org/Documentation/RTOS_book.html)
  - Language: C++ (Arduino)

  History
  Version YYYY-MM-DD Description
*/   
  String my_ver = "2.2.9";
/*  char my_ver[] = "2.2.1"; // Semantic Versioning (https://semver.org/)

    Given a version number MAJOR.MINOR.PATCH, increment the:
      MAJOR version when you make incompatible API changes,
      MINOR version when you add functionality in a backwards-compatible manner, and
      PATCH version when you make backwards-compatible bug fixes.

  ------- ---------- ---------------------------------------------------------------------------------------
  2.2.9   2019-01-04 - generate some telemetry data related to balancing every 4 milliseconds
          -re-enable the I value in PID - it had been previously commented out
          -todo: accelerometer calibration value? 
             remove crude compensation by +8 -done
             remove or fix pid_error_temp adjustment that's asymmetrical -done. removed
             reduce Pid_I_gain -done, from 1.2 to .4
             reduce Pid_D_gain - done, from 30 to 10
             consider re-introducing I_mem fading - deferred until more telemmetry analysed
             change bot_fast back to 250 for higher top end speed - test other changes first
             minimize impact of unstable angle_acc number. [only in anti drift calc (.996 x + .004 y)]
             clean out numchuk related code - mostly done
             set up balance point by:
                -getting bot at it's balance point (build a nifty jig?)
                -note value displayed on startup after text: "[initializeIMU_2]: Balance value...."
                -using this value in startWiFi() for MAC address 30:AE:A4:37:54:F8 for acc_calibration_value
                -this will result in the balance goal of zero degrees accurately reflecting off-center possibility
             move ISR param update until after the 4 Msec sync spin, for consistency (but a delay?)
             count step pulses per 4msec loop
             figure out why telemetry has long gaps of multiple 4msec intervals. PC? ESP32? algorithm?
             convert LINE() macro calls to LINE_TIME() which logs text arg and appends source code line and millis() - done
             allow robot to continue and balance if it can't find a WiFi network. see variable WiFi_active - done
             recreate the original "linear behaviour" for PID > wheel control mapping
             mount a Bobrow IMU for comparison / calibration
             add column titles and key parameter dump to telemetry data - done
             change wheel speed range to faster half of original range for more aggressive start
             map out Joop's pid to step count formulas for comparison
  2.2.8   2019-01-01 - return IMU warmup to 11 seconds so it's stable before calibration, 
          -split IMS initialization into two parts to allow network startup to run in parallel
          -add timeline macro to output timestamps + line numbers during setup()
          -add crude table of contents at top of file to help find routines in source code
          -simplify the I2C bus scan output,  discarding double dots.
          -do quicker speed changes by having balanceRobot zero the throttle_*_motor_memory variables
          -create LINET function that outputs string argument, followed by source code line number and milis timestamp
          -convert output of URL in startDNS to escape slashes so compiler won't think they're comments
          -move initializeIMU_1 earlier in setup to maximize overlapping processing, and minimize boot time
  2.2.7   2018-12-11 -add crude compensation for both gyro and accel angle measurements, because reading were off
          by 9 degees. also, gyro and accel don't agree - off by about 1.5 degrees
          -change bot fast speed control from 250 to 300 due to stalling motors
  2.2.6   2018-12-09 -reduce time spent in boot sequence from 42 to 13 seconds (to IP address display)
          -note for bot specific calibration purposes, original TWIPi has MAC address: 30:ae:a4:37:54:f8
          -remove 6 degree compensation after IMU fell off header during re-assembly
          -disable pid I memory fading
          -un-comment the setting of pid_i_mem. It was never being used our PID was actually PD.
          -now TWIPi's hyper reactive. reducing gain parameters. Originally 30, 1.5, 30
          -10, 1.2, 10: still seems to get into an oscillation. robot's right wheel making funny noises, even idle
          -bot_fast changed from 250 to 300, guessing oscillation is driving motors too fast
          -still getting oscillation at fast=400, but not at 500. 
          -some trace capability at 4 Msec level would really help, but difficult to capture
          -options to troubleshoot wheel noise:
              -swap position of DRV8825 & see if it changes wheels
              -swap stepper motors
              -scope out the control and power lines for that motor
              -use different GPIO's for step and dir on that wheel (hardware challenge)
              -try motors on a bench / breadboard system & see if problem can be reproduced, fixed...
              -research flakey GPio performance due to hidden Espressif activity
          -doesn't seem to be IMU, but could undo boot speed up changes to see if it makes a difference
  2.2.5   2018-12-08 -add 6 degree compensation for IMU mounting error
  2.2.4   2018-12-07 -recognize Doug's WiFi so boot up doesn't stall
          -fic esp32-hal-i2c.c in Doug's PlatformIO library to get timer0 interrupts to work for code from his PC
  2.2.3   2018-12-06 -recode the embedded web server html string so the compiler won't give errors
          -change string output in process_Client_JSON_msg to avoid compile errors
          -remove obsolete commented out code (can still be retrieved from previous versions)
  2.2.2   2018-11-28 Changed reference to Gyro and accelerometer sensors to jive with the new IMU 
          orientation inside the robot's chasis. X (roll) has become Y (pitch), Y (pitch) has become Z (Yaw).
          Also had to reverse the front and back motor rotation value to align with orientaiton of the motors 
          and IMU in the new chasis.  
  2.2.1   2018-11-25 Replaced all reference to TwoWire objects I2cOne and I2CTwo with Wire and Wire1 in an
          effort to remove hardware conflicts between timer0 and I2CTwo. This did not help. In the end the
          issues turned out to be a problem with the PlatformIO esp32-hal-i2c.c file. See issue Inconsistent 
          variable behavior #14 in our TWIPi repositories (https://github.com/va3wam/TWIPi/issues/14).
  2.2.0   2018-11-25 Altered setup() sequence and added mre LCD messages to track bootup. Also created 
          handles for FreeRTOS tasks created to run in different threads so we can reference them later.
  2.1     2018-11-14 Moved LED used for remote control from the built-in LED (13) to a pin for a seperate
          LED viewable outside the robot chasis (pin 15). Comments and variable name suggesting that we use
          the onboard or built-in LED are now misleading. Also moved motor pins to be compatible with the 
          TWIPI-PB1A-MIRROR board. NOTE, this code is MB1 compatable. To be MB2 compatible the motor
          pin numbers must be changed. 
  2.0     2018-10-11 Separated the I2C devices onto their own I2C bus. I2Cone has the LCD attached and 
          LCDtwo has the MPU attached to it.
  1.6     2018-04-13 The 1.5 fix made things worse. The error happend sooner. Commenting out WiFi all
          together to see if I2C becomes more reliable. The error is i2cWrite(): Busy Timeout! Addr: 68. 
          The I2C address 0x68 is assigned to the MPU6050 runing on the GY-521 board. This seems to have
          made the I2C bus communication reliable at last. Need to sort out how to have network services
          like WiFi, mDNS, websockets and web server running at the sae time without messing up the 
          reliability of the I2C bus. Also note that external 4.7K pull-up resistors were added around 
          version 1.4 and while they did not improve things they were left in and are part of the currently 
          stable configuration.
  1.5     2018-04-13 Pulled web service polling out of their own threads and put them in the main line in
          order to address an I2C error where the wire() calls result in a HAL error because the line is
          busy. The theory is that the WiFi activity is causing delays with writes and reads which cause 
          this error. There are others reporting issues like this and a new library fix is in the works to 
          address timing issues. 
  1.4     2018-04-13 Updated LINE macro to not TAB but rather label code line number more clearly. A cleanup
          of the short-cut macros would be handy as there is some redundancy now
  1.3     2018-04-02 Added motor control and PID logic from SBS Mark 2
  1.2     2018-04-01 Added DNS, Web and Websocket services
  1.1     2018-03-31 Moved init of IMU to its own FreeRTOS thread to and moved it up further in the boot 
          procss to allow for faster boot up by running the IMU init in parallel with other boot up tasks.
  1.0     2018-03-27 Code base created.
 ***********************************************************************************************************/

/***********************************************************************************************************
 Debug printing shortcuts.
 ***********************************************************************************************************/

#define LINE_TIME(name) sp(name); sp(" Line:");sp(__LINE__);sp(" millis:");spl(millis());
// convention is that on main entry to a routine, the text arg is in the format:
//      "<name of routine> general function."
// for subsequent calls providing more information, text arg is:
//      " [name of routine] event summary."
// note the leading space in above text arg, which indents entries other than main routine entrypoints

#define sp Serial.print                     // Shortform print no carrige return
#define spl Serial.println                  // Shortform print with carrige return
#define spc Serial.print(", ")              // Shortform print comma and space
#define spf Serial.printf                   // Shortform formatted printing with no line return
#define spdl(label,val) sp(label); spl(val) // Displays one labelled variable, ending with new-line 
                                            // example: spdl(" param2= ",param2);     
#define spd(label,val) sp(label); sp(val)   // Suitable for displaying multiple variables per line
                                            // example: spd("left motor= ",left_motor); 
                                            // spdl("  right motor= ",right_motor);
/***********************************************************************************************************
 Defines needed when using PLatformIO in Microsoft Visual Studio Code instead of the native Adduino IDE
 ***********************************************************************************************************/
#define LED_BUILTIN 15 // Pin that the onboard LED is connected to on the Huzzah32 board

/***********************************************************************************************************
 Define two I2C buses 
  I2C bus 1 (I2Cone): SDA1 on pin 23 and SCL1 on pin 22
  I2C bus 2 (I2Ctwo): SDA2 on pin 4 and SCL2 on pin 5
 ***********************************************************************************************************/
#define SDA1 23
#define SCL1 22
#define SDA2 4
#define SCL2 5

/***********************************************************************************************************
 Define timer0 variables and objects
 ***********************************************************************************************************/
#define timer_number_0 0 // Timer number can be 0 to 3, since we have 4 hardware timers on ESP32
#define timer_prescaler_0 80 // Prescaler, divides 80 MHz by 80 = 1 MHz, or interrupt every microsecond
hw_timer_t * timer0 = NULL; // Pointer used to configure the timer
portMUX_TYPE timerMux = portMUX_INITIALIZER_UNLOCKED; // Synchronize variable updates shared by ISR and main
#define timer_cnt_up true // Used to tell timer to count up
#define timer_cnt_down false // Used to tell timer to count down 
volatile long cntTimer0; 
volatile long t0_per_sec; 

/***********************************************************************************************************
 Define telemetry debug related variables
 ***********************************************************************************************************/
bool telClientConnected = false;  

/***********************************************************************************************************
 Define FreeRTOS task variables and objects
 ***********************************************************************************************************/
TaskHandle_t monWebSocket; // Handle for task that monitors webSockets
TaskHandle_t monWeb; // Handle for task that monitors HTTP 
TaskHandle_t monBalance; // Handle for task that balances robot
long cntBalance, cntLoop;    // not re-initialized, so not too useful

void flashLCD();  // from http://forum.arduino.cc/index.php?topic=42835.0
/***********************************************************************************************************
 Define motor control variables and constants
 ***********************************************************************************************************/
long pcnt; // This is used for some JSON message ping test timing
int acc_calibration_value; // Balance point of robot when balancing on its wheels (may not be vertical)
                           // To get this value, get the robot balancing, and watch the serial trace during boot up.
                           // Note that this variable is set in startWiFi() based on MAC address of ESP32.
                           // The MAC address read from the hardware selects one of these values:
int balance_37_54_f8 = 0;  // TWIPi MAC address: 30:AE:A4:37:54:F8 has this acc_calibration_value 

const volatile int speed = 1300; // for initial testing of interrupt driven steppers
//const volatile int speed = 200; // for initial testing of interrupt driven steppers
                               // speed = -1 enables IMU based balancing. 
                               // speed = n enables fixed forward speed interval of n
                               //         0 is brakes on
const int bot_slow = 1000; // # of interrupts between steps at slowest workable bot speed
const int bot_fast = 500; // # of interrupts between steps at fastest workable bot speed

/***********************************************************************************************************
 Define PID control variables and constants
 ***********************************************************************************************************/
/////////////////////////////////////////////////////////////////////////////////////////////////////////////
//Various PID settings
/////////////////////////////////////////////////////////////////////////////////////////////////////////////
// was 30, 1.2, 30 before 2018-12-10
// back to above 2018-12-11
// based on telemetry, on jan 7: 15, 0.4, 10
float pid_p_gain = 15;          // Gain setting for the P-controller (15)
float pid_i_gain = 0.0;         // Gain setting for the I-controller (1.5)
float pid_d_gain = 0.0;         // Gain setting for the D-controller (30)
const long usec_per_t0_int = 20; // Number of microseconds between t0 timer interrupts
const int pid_max = 400;        // Upper bound for pid values
const int pid_min = -400;       // Lower bound for pid values
const float PID_I_fade = .80;   // How much of pid_i_mem history to retain

/////////////////////////////////////////////////////////////////////////////////////////////////////////////
// Define the GPIO pins that perform functions on DVR8825 motor controller. Changed as follows:
// Left step moved from 12 to 32
// Left dir stays the same at 14 
// Right step moved from 15 to 26
// Right dir moved from 13 to 25
/////////////////////////////////////////////////////////////////////////////////////////////////////////////
#define pin_left_step 32  // GPIO 32 initiates a step on motor on robot's left side 
#define pin_left_dir 14 // GPIO 14 controls the direction of left motor
#define pin_right_step 26 // GPIO 26 initiates a step on motor on robot's right side
#define pin_right_dir 25 // GPIO 25 controls the direction of right motor

/////////////////////////////////////////////////////////////////////////////////////////////////////////////
//Declaring global variables and setting some values (YABR cut and paste)
/////////////////////////////////////////////////////////////////////////////////////////////////////////////
byte start;    // controls whether or not we've moving wheels to attempt to balance the robot
               // initially 0, set to 1 when robot angle is close to zero, set back to 0 if offset exceeds 30 degrees
volatile int left_motor, throttle_left_motor, throttle_counter_left_motor, throttle_left_motor_memory;
volatile int right_motor, throttle_right_motor, throttle_counter_right_motor, throttle_right_motor_memory;
int receive_counter;
int gyro_pitch_data_raw, gyro_yaw_data_raw, gyro_roll_data_raw, accelerometer_data_raw;
long gyro_yaw_calibration_value, gyro_pitch_calibration_value, balance_calibration_value, gyro_roll_calibration_value;
unsigned long loop_timer;
float angle_gyro, angle_acc, angle;
float pid_error_temp, pid_i_mem, gyro_input, pid_output, pid_last_d_error;
float pid_output_left, pid_output_right;
float hold, hold1, hold2, hold3, hold4, hold5;
long mics, loop_mics, last_millis; // Measure length of balanceRobot() loop, and print occasionally
int t0_count;
long t,t_old,d;
int millis_now, i=1;
long mil, mic;
volatile long int_time;
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
void loop() 
{
    cntLoop++;

    balanceRobot();
/*
    Serial.print("t0_per_sec = ");
    Serial.print(t0_per_sec);
    Serial.print(" cntTimer0 = ");
    Serial.print(cntTimer0);
    Serial.print(" cntBalance = ");
    Serial.print(cntBalance);
    Serial.print(" cntLoop = ");
    Serial.println(cntLoop);
*/
} //loop()

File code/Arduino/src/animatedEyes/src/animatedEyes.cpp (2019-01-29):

#include <Arduino.h>
#include <amDisplayRunningConfiguration.h> // Library class that dislays useful info about this sketch
#include <Adafruit_SSD1306.h> // https://github.com/adafruit/Adafruit_SSD1306
#include <Adafruit_GFX.h> // https://github.com/adafruit/Adafruit-GFX-Library
#include <Wire.h> // For I2C buses
#include <normalEye.h> // Using this to figure put process for using custom images for OLED
/***********************************************************************************************************
  Synopsis:
  This sketch is being used to come up with the most effective eye animations for a pair of OLED displays 
  that will be used on the TWIPi class robots. Maybe try the U8glib2 library rather than the Adafruit_GFX
  library since we are having so much trouble getting images to display properly. The approach we are going 
  to try is outlined at this site: 
  https://sandhansblog.wordpress.com/2017/04/16/interfacing-displaying-a-custom-graphic-on-an-0-96-i2c-oled/  
  which has some details on using GIMP to create images and export using the X Bitmap format (.xbm).
  
  NOTE!!! /Users/andrewmitchell/.platformio/packages/framework-arduinoespressif32/cores/esp32/esp32-hal-i2c.c
  has custom lines in it that differ from the ESP-IDF stable release. Make sure that these lines are 
  maintained when updating to the latest PlatformIO ESP-IDF files. Failure to do so will result in unrelaible
  I2C and hardware timer behavior. See the clsojng comments for issue https://github.com/va3wam/TWIPi/issues/14
  for full details.

  Environment:
  - Visual Source Code with PlatformIO plugin
  - Platform: Espressif 32 (https://www.espressif.com/en/products/hardware/esp32/overview)
  - Framework: Arduino 
  - Embedded board: Adafruit HUZZAH32 Feather (https://learn.adafruit.com/adafruit-huzzah32-esp32-feather/pinouts)
  - SOC: WROOM32 module (https://dl.espressif.com/doc/esp-idf/latest/hw-reference/modules-and-boards.html)
  - IDE: Visual Studio Code v1.27.2 (https://code.visualstudio.com/)
  - VSC plugin: platformIO v3.6.1a4 (https://platformio.org/platformio-ide)
  - RTOS: FreeRTOS (https://www.freertos.org/Documentation/RTOS_book.html)
  - Language: C++ (Arduino)

  Hardware:
  - Adafruit OLED
    Dimensions: 0.96inch
    Resolution: 128×64 Pixels
    I2C address: 0x7A or 0x7B depending on resistor placement
    Arduino Library: Adafruit_SSD1306.cpp (graphics) and Adafruit_SSD1306.h (communication)
    Operating voltage: 3-5V

  History
*/   
  char my_ver[] = "1.0.0"; // Semantic Versioning (https://semver.org/)
/*
  Version YYYY-MM-DD Description
  ------- ---------- ---------------------------------------------------------------------------------------
  1.0.0   2018-12-02 Code base created.
 ***********************************************************************************************************/
amDisplayRunningConfiguration aboutThisSketch(my_ver); // Define a function that displays info about this 
                                                       // sketch

/***********************************************************************************************************
 Define first I2C bus and associated constants and global variables. SDA1 is on GPIO 23 (physical pin 17) 
 and SCL1 is on GPIO pin 22 (physical pin 18). 
 ***********************************************************************************************************/
#define SDA1 23 // Define SDA I2C pin for first I2C bus (wire)
#define SCL1 22 // Define SCL I2C pin for first I2C bus (wire)

/***********************************************************************************************************
 Define OLED constants and global variables. 
 ***********************************************************************************************************/
#define SCREEN_WIDTH 128 // OLED display width, in pixels
#define SCREEN_HEIGHT 64 // OLED display height, in pixels
// Declaration for an SSD1306 display connected to I2C (SDA, SCL pins)
#define OLED_RESET     4 // Reset pin # (or -1 if sharing Arduino reset pin)
Adafruit_SSD1306 rightOLED(SCREEN_WIDTH, SCREEN_HEIGHT, &Wire, OLED_RESET); // Define right OLED object
Adafruit_SSD1306 leftOLED(SCREEN_WIDTH, SCREEN_HEIGHT, &Wire, OLED_RESET); // Define left OLED object
#define LOGO_HEIGHT   64
#define LOGO_WIDTH    88
int rightOLED_I2C_Address = 0x3C; // I2C address of right OLED display (robot perspective)
int leftOLED_I2C_Address = 0x3D; // I2C address of left OLED display (robot perspective)

/***********************************************************************************************************
 This function initializes the console where trace information is sent during sketch execution.
 ***********************************************************************************************************/
void initConsole()
{
  Serial.begin(115200); //NOTE: Be sure to put monitor_speed = 115200 in platformio.ini
  delay(5); //Give serial time to initialize before using it
  Serial.println("[initConsole] **************************************************************************"); 
} //initConsole()

/***********************************************************************************************************
 This function dumps a bunch of useful info to the terminal. NOte that an effort has been made to put
 most of the printing of key data into the class amDisplayRunningConfiguration() but some data must be
 generated inside this sketch to get the correct information abot this sketch and not the class file. This 
 is why the file name and line number informaiton must be called from this routine and not the class.
 ***********************************************************************************************************/
void display_Running_Sketch()
{
  Serial.print("[display_Running_Sketch] Start of sketch. Source code line: ");
  Serial.println(__LINE__); //Get currrent line of code being executed
  Serial.print("[display_Running_Sketch] Sketch Name: ");
  Serial.println(__FILE__); //Get file name of sketch being run
  aboutThisSketch.display(); // Show additional information about this sketch in the console
} //display_Running_Sketch()
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

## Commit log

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2018-09-19 fix LCD header, as decoupling caps
    [twip-mb1.brd, twip-mb1.sch]
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2018-09-24 checkpoint as of 2018-09-24
    Sep 24 checkpoint has mutually consistent versions of MB and PB layouts, and pinouts documentation
    [pinouts.ods]
2018-09-24 Sep 24 checkpoint has mutually consistent versions of MB and PB layouts, and pinouts documentation
    completed layout of peripheral board, with a few retrofits to MB for IBC connector changes. Added a 4 position DIP switch to PB as a way to have jumpers that cross other traces, as I couldn't quite do a single sided layout. All switches go to the right when active, and the voltage regulators, whose 4 legs are represented by two 5 pin headers, are correctly scaled. I'd like to space out the top connector for the stepper motor connections, but the board is at the max size allowed, and Eagle CAD won't allow it to be moved upward.
    [twip-mb1.brd, twip-mb1.sch, twip-pb1A.brd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]
2018-09-26 minor layout fixes
    need to use version numbers built into copper plate.
    [twip-mb1.brd, twip-pb1A.brd]
2018-09-27 minor fixes, and upsized boards to 3.3 x 5 inches
    [twip-mb1.brd, twip-pb1A.brd]
2018-10-11 Split LCD and MPU onto their own I2C buses to avoid conflicts
    [main.ino]
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2018-10-31 Out of date, new file replaces called 1A this
    [twip-pb1.brd]
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2018-11-01 Moved files to new directories and added ATC files for peripheral board
    [ConvertFlatCAMgcode.ods, Tormach-Machine-Codes.ods, cad-conversions.ods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]
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2018-11-04 last parts list update didn't work
    [parts-list.ods]
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2018-11-14 new MB2 layout that isn't s/w compatible
    new layout of the main board with these changes:
    -change power for front panel LCD from 3.3 to 5 volts
    -minor changes for more soldering room around component leads
    -software controlled LED moved from GPio 36 (which is input only) to GPio 15
    -in order to be able to route above change, had to move 2 motor control signals:
    need to change the GPio pins used for STEP and DIR on the motor controller for the robot’s left wheel.
    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
    [twip-mb2.brd, twip-mb2.sch]
2018-11-14 proposed way to fix bad S/W LED GPio choice
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2018-11-16 Struggling to create correct directory structure
    [main.ino]
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2018-11-17 Create software-led-fix.odg
    minor update, if any
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2018-11-26 Working on Timer0 bug
    Many code chnages made as I isolate the cause of the conflict between the second I2C bus and Timer0
    [main.cpp, main.ino]
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2018-11-28 Fixed issue with timer and I2C bus
    Interrupt resource limitation in I2C library sorted out.
    [main.cpp, main.ino]
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2018-11-30 Update twip-pb1A.brd
    bridge 5V grounds to get console working on battery power
    [twip-pb1A.brd]
2018-11-30 Update twip-pb1A.sch
    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
    [twip-pb1A.sch]
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2018-12-05 Update main.ino
    reworked coding of embedded HTML, and fixed some debug output that caused compile errors
    [main.ino]
2018-12-06 Update main.ino
    remove obsolete comented out code, including Twowire references that have been replaced by Wire references
    [main.ino]
2018-12-08 Update main.ino
    add support for Doug's home Wifi so boot up won't stall. Fix PlatformIO hal I2C library on Doug's PC to get timero interrupts working
    [main.ino]
2018-12-11 Update main.ino
    reduce boot time, fix pid_i_mem disabled, play with PID gain numbers and motor speed limits, undo 6 degree compensation after IMU was remounted
    [main.ino]
2018-12-11 Update main.ino
    crude compensation for large errors in IMU readings, reduce top speed from 250 to 300.
    [main.ino]
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2018-12-19 Deleted old telemtry files from Java client
    We will no longer use this. In future do not use special characters in file names as it upsets Windows
    [tl-20181219121228.csv]
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2018-12-20 Delete pinouts.ods
    replaced by hardware version specific pinout files
    [pinouts.ods]
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2018-12-21 Update twip-pb2.brd
    latest flavour with power and stepper headers at back of bot
    [twip-pb2.brd]
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2018-12-24 Create LED-resistors.ods
    LED resistors are a bit more complicated because different colours have different voltage drops.
    [LED-resistors.ods]
2018-12-24 Create parts-list - hw-ver2.ods
    starting a parts list for MB2 + PB2 + latest chassis
    [parts-list - hw-ver2.ods]
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2018-12-24 Update twip-mb2.brd
    big changes to IBC pinouts to shift stepper connectors around
    [twip-mb2.brd]
2018-12-24 Update twip-mb2.sch
    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
    [twip-mb2.sch]
2018-12-24 Update twip-pb2.sch
    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
    [twip-pb2.sch]
2018-12-24 Update twip-pb2.brd
    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
    [twip-pb2.brd]
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2018-12-29 Update pinouts-hw-ver2.ods
    up to date for MB2 and PB2, but more changes expected
    [pinouts-hw-ver2.ods]
2018-12-29 Update twip-mb2.brd
    fix USB data connections
    [twip-mb2.brd]
2018-12-29 Update twip-pb2.brd
    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
    [twip-pb2.brd]
2018-12-29 Update twip-pb2.sch
    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
    [twip-pb2.sch]
2019-01-01 Update led-resistors.odg
    led-resistors.odg is obsolete, replaced by more accurate and comprehensive LED-resistors.ods
2019-01-01 Update LED-resistors.ods
    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
    [LED-resistors.ods]
2019-01-01 Update pinouts-hw-ver2.ods
    separated out components to individual sheets, and updated to reflect latest board changes
    [pinouts-hw-ver2.ods]
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2019-01-01 Update twip-mb2.brd
    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
    [twip-mb2.brd]
2019-01-01 Update twip-mb2.sch
    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
    [twip-mb2.sch]
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2019-01-02 Create HW-V2-Todos.ods
    Doug's list of completed and suggested changes for the MB2/PB2 combination
    [HW-V2-Todos.ods]
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2019-01-03 speeding up IMU boot
    fix new imu initialization, added timeline debug lines
    [main.ino]
2019-01-08 many changes and cleanups per 2.2.9 version notes
    quite a few fixes, PID returning based on telemetry analysis, and several new features.
    [main.ino]
2019-01-08 implications of some code bugs illustrated
    all discovered bugs fixed in source code
    [annotated-telemetry-2018-01-06-0100.ods]
2019-01-16 pid vs speed vs Joop calcs
    pid vs speed vs Joop calcs
    [pid_calculations.ods]
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2019-01-20 new sheet with tilt torque calculations
    3rd sheet shows tilt torque calculations for angles from 1 to 20 degrees
    [torque-measurements.ods]
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2019-02-13 more info on etch widths
    Our traces that carry 12+ volts, and grounds seem to need to be wider to carry the current. references and calcs are in 2nd and 3rd sheets.
    [cad-conversions.ods]
2019-02-13 didn't mean to change this?
    [twip-mb-mirror.brd]
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2019-02-13 attempted redesign with DRVs moved
    never completed - going with single board design
    [twip-mb3.brd]
2019-02-13 redesign with DRV's moved
    never completed - moved to single board design
    [twip-mb3.sch]
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2019-02-13 new design - top half of single board design
    never completed - moving to single board design
    [twip-mb4.brd]
2019-02-13 new design using top half of single board design
    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
    [twip-mb4.sch]
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2019-03-13 Syncronizing Fusion and Eagle board
    Ongoing syncronizing of mounting crew hle positions
    [copper_bottom.gbr, copper_top.gbr, drills.xln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]
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2019-03-17 finalization of single board design, plus remoted switches and usb jack
    finalization of single board design, plus remoted switches and usb jack
    [sb3.brd]
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2019-05-01 minor fixes before release to manufacturing
    [sb3.sch]
2019-05-01 final fixesbefore release to manufacturing
    [sb3.brd]
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2019-06-15 fix plu spacing issues found in flatcam
    version P2 of PLU has a bunch of fixes to fix places where there were passages between traces, or between traces and pads that were too narrow for a 1/32 inch mill bit to pass through. 2 weren't fixable, and I added jumpers to dodge the issue. The rest of the 7 issues were resolved by small adjustments to trace locations
    [plu.brd, plu.sch]
2019-06-15 Created DXF file for PLU board
    This DXF file is created as part of the process of creating the CAD and CAM files to mill the PCB
    [plu.dxf]
2019-06-16 PLU board release 2D
    The release for PLU board is a set of 4 synchronized files. Filenames are plu-rel2d, and extensions are brd, sch, dwf, and png. The png one is a Irfanview display of the DXF files illustraing that th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
    [plu - Copy.brd, plu - Copy.sch, plu-rel2d.brd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]
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2019-06-18 Create plu-rel2d.dxf
    Re-ran the DXF extract for the PLU-rel2 board. Needed to chnage units from mm to inches
    [plu-rel2d.dxf]
2019-06-18 Update drill-list.ods
    Added details of drills we have and which ones we will use to make the plu_rel2 board.
    [drill-list.ods]
2019-07-01 fix sb5 pads, document eagle dxf pads bug
    [plu-first.dxf, plu.dxf, sb5-nofix.dxf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]
2019-07-02 show actuial part numbers ordered
    new column shows parts ordered from DigiKey
    [sb5-parts.ods]
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2019-07-07 sb6 = doublesided sb5
    got rid of 8 jumpers, and 16 holes by gping doublesided so jumpers could be done in etches. vias all done at component legs, and need careful attention at soldering time. the "pads" version has all pads fixed.
    [sb6.brd, sb6.sch, sb6pads.brd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]
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2019-07-18 make a dxf file - seems to cause a lot of changes
    [sb6pads.dxf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]
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2019-10-09 Revert "general update"
    This reverts commit a1f0684ff9991b19a33d9eab397e4021da647801.
    [ConvertFlatCAMgcode.ods, parts-list - hw-ver2.ods, parts-list.ods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]
2019-12-11 update during board testing
    Platform.io upgrade caused a bunch of changes, but there are some board documentation changes as well.
    [sb3-pinouts.ods, sb6-parts2.ods]
2020-01-24 New SB7 - combined board
    Single double sided board with cpu, IMU, Motor controllers, etc, as well as the 4 pushbutton controls and USB jack. Assumes off-board power regulation for 12 and 5 volts.
    [sb7-parts.ods, sb7-pinouts.ods, sb7pads - 7A.brd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]
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2020-02-20 Updated SB7 with new connectros and traces
    This is the version being sent to PCBWay for manufacturing. It includes a new USB connector for the Huzzah32 board, new power connectors as well as a new trace for interrupts from the MPU6050 on the 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
    [sb7pads-7D.brd, sb7pads-7D.sch]
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
